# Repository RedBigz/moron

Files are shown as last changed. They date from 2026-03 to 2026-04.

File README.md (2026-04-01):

<p align="center">
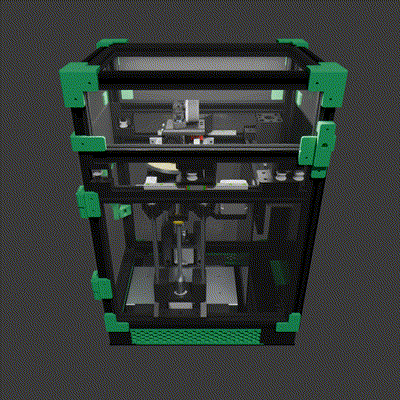
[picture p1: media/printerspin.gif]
    
</p>

<h1 align="center">Moron - The "Non-Euclidean" "V0"</h1>

| [JOURNAL](JOURNAL.md) *(48.5h)* | ~~[BUILDING JOURNAL](JOURNAL_BUILDING.md)~~ | [BOM](BOM.csv) |
|---|---|---|

# Introduction

Hello! I'm May, and you're witnessing the best creation known to man. I don't know how I'm getting a grant for this, but free printer money is free printer money.

> firmware would be an absolute mess<br>
> \- Anicetus 2026

The Moron is a Polar-CoreXY hybrid printer that looks like a V0. I call it "non-euclidean" because I plan to use the polar bed for arc moves -- therefore the best distance between two points is not a straight line.

I wanted something silly that could print ASA and mess around with. Sporting a 120mm polar bed and a 120x120x120 volume, what is there to not like? I haven't written the kinematics yet in software (famous last words -- and I kind of need the printer to do that lol), but right now I bet you could get some really cool timelapses!

My aim for the project is to design a very... odd, printer haha. I also need an enclosed printer for ASA among other things, so this would be a very big help for future projects!

If you want to build one: *don't*. But if you're redbigz you can find all the subtractive cuts/heater files in `cad/cuts/` and `cad/pcb/` and the CAD link [here](https://cad.onshape.com/documents/feabf94b86e21fadd98f4223/w/96543d883315d41072e87b21/e/ef18f69e66a19900010b1f70) (oh also the final STEP is in `cad/`!).

**Forgot to mention this, but please check out the [Voron V0](https://vorondesign.com/voron0.2)! It was a massive inspiration when designing the Moron (from the frame to the electronic placement), so it deserve credit.**

# Render Gallery

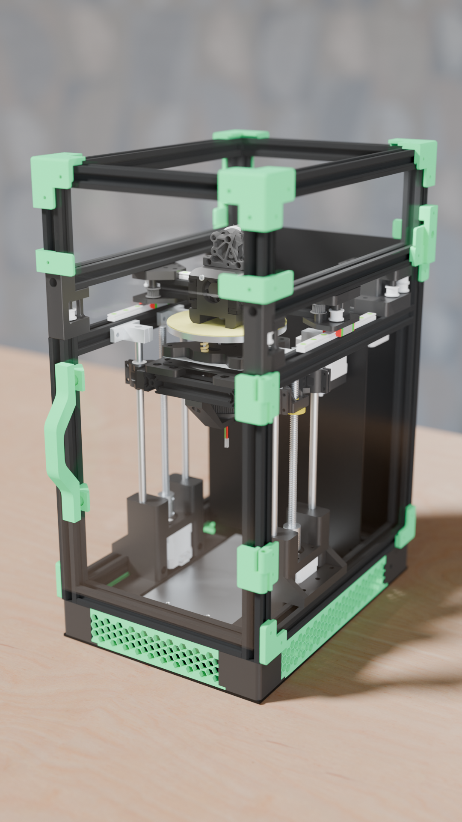
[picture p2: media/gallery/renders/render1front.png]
Render 1 - Front

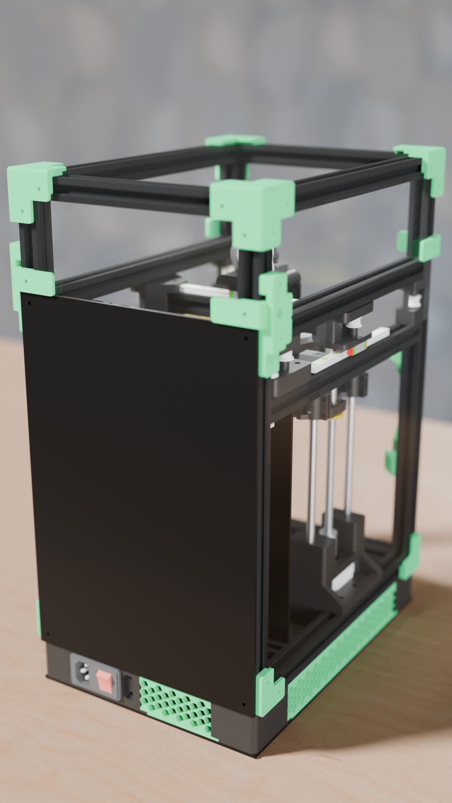
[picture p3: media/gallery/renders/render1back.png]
Render 1 - Back


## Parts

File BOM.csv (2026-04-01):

Category | Cat. 2 | Product | Size | Sourcing Method | Price (USD) | Shipping (USD) | GST (USD) | Qty | Total (USD) | Link | % of Grant | Grant Money Left | % of Grant Money Left
Exterior |  |  |  |  |  |  |  |  |  |  | 0.00% | $350.00 | 100.00%
 | Panels |  |  |  |  |  |  |  |  |  | 0.00% | $350.00 | 100.00%
 |  | Acrylic | 860x630mm | Self | $0.00 | $0.00 | $0.00 | 1 | $0.00 |  | 0.00% | $350.00 | 100.00%
 |  | Flute Board | 900x600mm | Self | $0.00 | $0.00 | $0.00 | 1 | $0.00 |  | 0.00% | $350.00 | 100.00%
 | Etc. |  |  |  |  |  |  |  |  |  | 0.00% | $350.00 | 100.00%
 |  | Magnet | 10x2mm | AliExpress | $5.60 | $0.00 | $0.56 | 1 | $6.16 | https://www.aliexpress.com/item/1005011864346920.html | 1.76% | $343.84 | 98.24%
Internals |  |  |  |  |  |  |  |  |  |  | 0.00% | $343.84 | 98.24%
 | Frame |  |  |  |  |  |  |  |  |  | 0.00% | $343.84 | 98.24%
 |  | Gantry Extrusions | 1600mm |  |  |  |  |  |  |  | 0.00% | $343.84 | 98.24%
 |  | Bed Extrusions | 400mm |  |  |  |  |  |  |  | 0.00% | $343.84 | 98.24%
 |  | Main Extrusions | 2250mm |  |  |  |  |  |  |  | 0.00% | $343.84 | 98.24%
 |  | Top Hat Extrusions | 1400mm |  |  |  |  |  |  |  | 0.00% | $343.84 | 98.24%
 |  | Total Extrusions | 4800mm | AliExpress | $48.61 | $4.35 | $5.30 | 1 | $58.26 | https://www.aliexpress.com/item/1005003428294239.html | 16.64% | $285.58 | 81.60%
 |  |  | 900mm | Self | $0.00 | $0.00 | $0.00 | 1 | $0.00 |  | 0.00% | $285.58 | 81.60%
 |  | T-Nut (30pcs/lot) | M3 | AliExpress | $3.38 | $0.00 | $0.34 | 2 | $7.44 | https://www.aliexpress.com/item/1005010661007823.html | 2.12% | $278.15 | 79.47%
 |  |  | M5 | Self | $0.00 | $0.00 | $0.00 | 2 | $0.00 |  | 0.00% | $278.15 | 79.47%
 |  | Furniture Pad Sheet | ? | Self | $0.00 | $0.00 | $0.00 | 1 | $0.00 |  | 0.00% | $278.15 | 79.47%
 |  |  |  |  |  |  |  |  |  |  | 0.00% | $278.15 | 79.47%
 | Gantry |  |  |  |  |  |  |  |  |  | 0.00% | $278.15 | 79.47%
 |  | Idlers | 20TW6B5 | Self | $0.00 | $0.00 | $0.00 | 1 | $0.00 |  | 0.00% | $278.15 | 79.47%
 |  |  | 20TW6B5 | AliExpress | $6.06 | $0.00 | $0.61 | 1 | $6.67 | https://www.aliexpress.com/item/1005007557987612.html | 1.90% | $271.48 | 77.57%
 |  | Pulleys | 6mm | Self | $0.00 | $0.00 | $0.00 | 1 | $0.00 |  | 0.00% | $271.48 | 77.57%
 |  | Dowel Pins | M5 | Self | $0.00 | $0.00 | $0.00 | 1 | $0.00 |  | 0.00% | $271.48 | 77.57%
 |  | Linear Rail | MGN9H 150mm | AliExpress | $11.21 | $0.00 | $1.12 | 3 | $36.99 | https://www.aliexpress.com/item/1005008170521006.html | 10.57% | $234.49 | 67.00%
 |  | Timing Belt | 6mm 2m | AliExpress | $2.77 | $0.00 | $0.28 | 1 | $3.05 | https://www.aliexpress.com/item/1005005216868552.html | 0.87% | $231.44 | 66.13%
 |  | Motors | 17HS4401 | AliExpress | $7.48 | $0.00 | $0.75 | 2 | $16.46 | https://www.aliexpress.com/item/1005004586903773.html | 4.70% | $214.99 | 61.42%
 |  |  |  |  |  |  |  |  |  |  | 0.00% | $214.99 | 61.42%
 | Toolhead |  |  |  |  |  |  |  |  |  | 0.00% | $214.99 | 61.42%
 |  | Gearset Kit | - | AliExpress | $13.50 | $0.00 | $1.35 | 1 | $14.85 | https://www.aliexpress.com/item/1005004699143725.html | 4.24% | $200.14 | 57.18%
 |  | Extruder Motor | NEMA14 | AliExpress | $10.66 | $0.00 | $1.07 | 1 | $11.73 | https://www.aliexpress.com/item/1005006423228157.html | 3.35% | $188.41 | 53.83%
 |  | Part Cooling Fan (2pcs/lot) | 3010 | AliExpress | $4.21 | $0.00 | $0.42 | 1 | $4.63 | https://www.aliexpress.com/item/1005009389076562.html | 1.32% | $183.78 | 52.51%
 |  | Heatsink Fan | 3010 Axial | AliExpress | $3.05 | $0.00 | $0.31 | 1 | $3.36 | https://www.aliexpress.com/item/1005008793365820.html | 0.96% | $180.42 | 51.55%
 |  | TZ V6 2.0 | - | AliExpress | $15.33 | $0.00 | $1.53 | 1 | $16.86 | https://www.aliexpress.com/item/1005011904542108.html | 4.82% | $163.56 | 46.73%
 |  | BiQu Microprobe |  | AliExpress | $18.32 | $0.00 | $1.83 | 1 | $20.15 | https://www.aliexpress.com/item/1005006314165426.html | 5.76% | $143.41 | 40.97%
 |  |  |  |  |  |  |  |  |  |  | 0.00% | $143.41 | 40.97%
 | Z Axis |  |  |  |  |  |  |  |  |  | 0.00% | $143.41 | 40.97%
 |  | A Motor | 17HS4023 | AliExpress | $5.47 | $0.00 | $0.55 | 1 | $6.02 | https://www.aliexpress.com/item/1005003874936862.html | 1.72% | $137.39 | 39.25%
 |  | Closed Loop Timing Belt | 2GT 6mm 320mm | AliExpress | $4.66 | $0.00 | $0.47 | 1 | $5.13 | https://www.aliexpress.com/item/1005006817234108.html | 1.46% | $132.27 | 37.79%
 |  | Slip Ring | 2.5mm 4CH 5A | AliExpress | $11.25 | $0.54 | $1.18 | 1 | $12.97 | https://www.aliexpress.com/item/1005007456626183.html | 3.71% | $119.30 | 34.08%
 |  | Bed | 120mm (1070 Al) | AliExpress | $9.77 | $0.00 | $0.98 | 1 | $10.75 |  | 3.07% | $108.55 | 31.01%
 |  | Heater |  | JLC | $3.00 | $6.00 | $0.00 | 1 | $9.00 |  | 2.57% | $99.55 | 28.44%
 |  | Bed Springs | ? | AliExpress | $2.90 | $0.00 | $0.29 | 1 | $3.19 | https://www.aliexpress.com/item/1005010253928500.html | 0.91% | $96.36 | 27.53%
 |  | Lead Screw | - | Self | $0.00 | $0.00 | $0.00 | 1 | $0.00 |  | 0.00% | $96.36 | 27.53%
 |  | Coupler | SK8 | Printed | $0.00 | $0.00 | $0.00 | 1 | $0.00 |  | 0.00% | $96.36 | 27.53%
 |  | Smooth Rods | - | Self | $0.00 | $0.00 | $0.00 | 1 | $0.00 |  | 0.00% | $96.36 | 27.53%
 |  | Bearings (4pcs/lot) | LM8UU | AliExpress | $10.56 | $0.00 | $1.06 | 1 | $11.62 | https://www.aliexpress.com/item/1005009031115995.html | 3.32% | $84.74 | 24.21%
 |  | Lazy Susan | 4” | AliExpress | $3.30 | $0.00 | $0.33 | 1 | $3.63 | https://www.aliexpress.com/item/4001325945215.html | 1.04% | $81.11 | 23.18%
 |  | Round PEI Sheet | 120mm + Base | AliExpress | $14.36 | $0.00 | $1.44 | 1 | $15.80 | https://www.aliexpress.com/item/1005006173526115.html | 4.51% | $65.32 | 18.66%
 |  | Silicone Wire | 16AWG 2M | AliExpress | $3.83 | $0.00 | $0.38 | 1 | $4.21 | https://www.aliexpress.com/item/1005008563402600.html | 1.20% | $61.11 | 17.46%
 |  | Z Motors | 17HS4401 | Self | $0.00 | $0.00 | $0.00 | 2 | $0.00 |  | 0.00% | $61.11 | 17.46%
 |  |  |  |  |  |  |  |  |  |  | 0.00% | $61.11 | 17.46%
 | Electronics |  |  |  |  |  |  |  |  |  | 0.00% | $61.11 | 17.46%
 |  | Mean Well LRS-350 | 24V | AliExpress | $30.63 | $2.16 | $3.28 | 1 | $36.07 | https://www.aliexpress.com/item/1005005439330497.html | 10.31% | $25.04 | 7.15%
 |  | TMC2209 (6pcs/lot) | - | AliExpress | $21.40 | $0.00 | $2.14 | 1 | $23.54 | https://www.aliexpress.com/item/33028050145.html | 6.73% | $1.50 | 0.43%
 |  | Mellow FLY D7 | - | AliExpress | $22.84 | $0.00 | $2.28 | 1 | $25.12 | https://www.aliexpress.com/item/1005006422323624.html | 7.18% | -$23.63 | -6.75%
 |  | USB C Mount | 50cm | AliExpress | $2.80 | $0.00 | $0.28 | 1 | $3.08 | https://www.aliexpress.com/item/1005007625403004.html | 0.88% | -$26.71 | -7.63%
 |  | Electronics Fan | ? | Self | $0.00 | $0.00 | $0.00 | 1 | $0.00 |  | 0.00% | -$26.71 | -7.63%
 |  |  |  |  |  |  |  |  |  |  | 0.00% | -$26.71 | -7.63%
 | Fasteners |  |  |  |  |  |  |  |  |  | 0.00% | -$26.71 | -7.63%
 |  | Fasteners | M2.5x8mm | AliExpress | $1.76 | $0.00 | $0.18 | 1 | $1.94 | https://www.aliexpress.com/item/1005005070119421.html | 0.55% | -$28.64 | -8.18%
 |  |  | M3/M4/M5 | Self | $0.00 | $0.00 | $0.00 | ? | $0.00 |  | 0.00% | -$28.64 | -8.18%
 |  | Heated Inserts | M3L3OD4.5 | AliExpress | $3.29 | $0.00 | $0.33 | 1 | $3.62 | https://www.aliexpress.com/item/1005006838108683.html | 1.03% | -$32.26 | -9.22%
 |  |  | M4L4OD6 | AliExpress | $4.87 | $0.00 | $0.49 | 1 | $5.36 |  | 1.53% | -$37.62 | -10.75%
 |  |  |  |  |  |  |  |  |  |  | 0.00% | -$37.62 | -10.75%
Other |  |  |  |  |  |  |  |  |  |  | 0.00% | -$37.62 | -10.75%
 | Tools |  |  |  |  |  |  |  |  |  | 0.00% | -$37.62 | -10.75%
 |  | Tap | M5x0.8mm | AliExpress | $2.45 | $0.00 | $0.25 | 1 | $2.70 | https://www.aliexpress.com/item/33056326494.html | 0.77% | -$40.32 | -11.52%
 |  |  |  |  |  |  |  |  |  |  | 0.00% | -$40.32 | -11.52%
 | Filament |  |  |  |  |  |  |  |  |  | 0.00% | -$40.32 | -11.52%
 |  | PETG (I know I should use ASA but I don’t have a good space to print it) | Black | Self | $0.00 | $0.00 | $0.00 | 1 | $0.00 |  | 0.00% | -$40.32 | -11.52%
 |  | PLA+ (external use only) | Mint Green | Self | $0.00 | $0.00 | $0.00 | 1 | $0.00 |  | 0.00% | -$40.32 | -11.52%
 |  | Bowden Tube | 1.75mm 1M | Self | $0.00 | $0.00 | $0.00 | 1 | $0.00 |  | 0.00% | -$40.32 | -11.52%
Total |  |  |  |  |  |  |  |  | $390.32
Grant |  |  |  |  |  |  |  |  | $350.00
Out-of-Pocket |  |  |  |  |  |  |  |  | $40.32

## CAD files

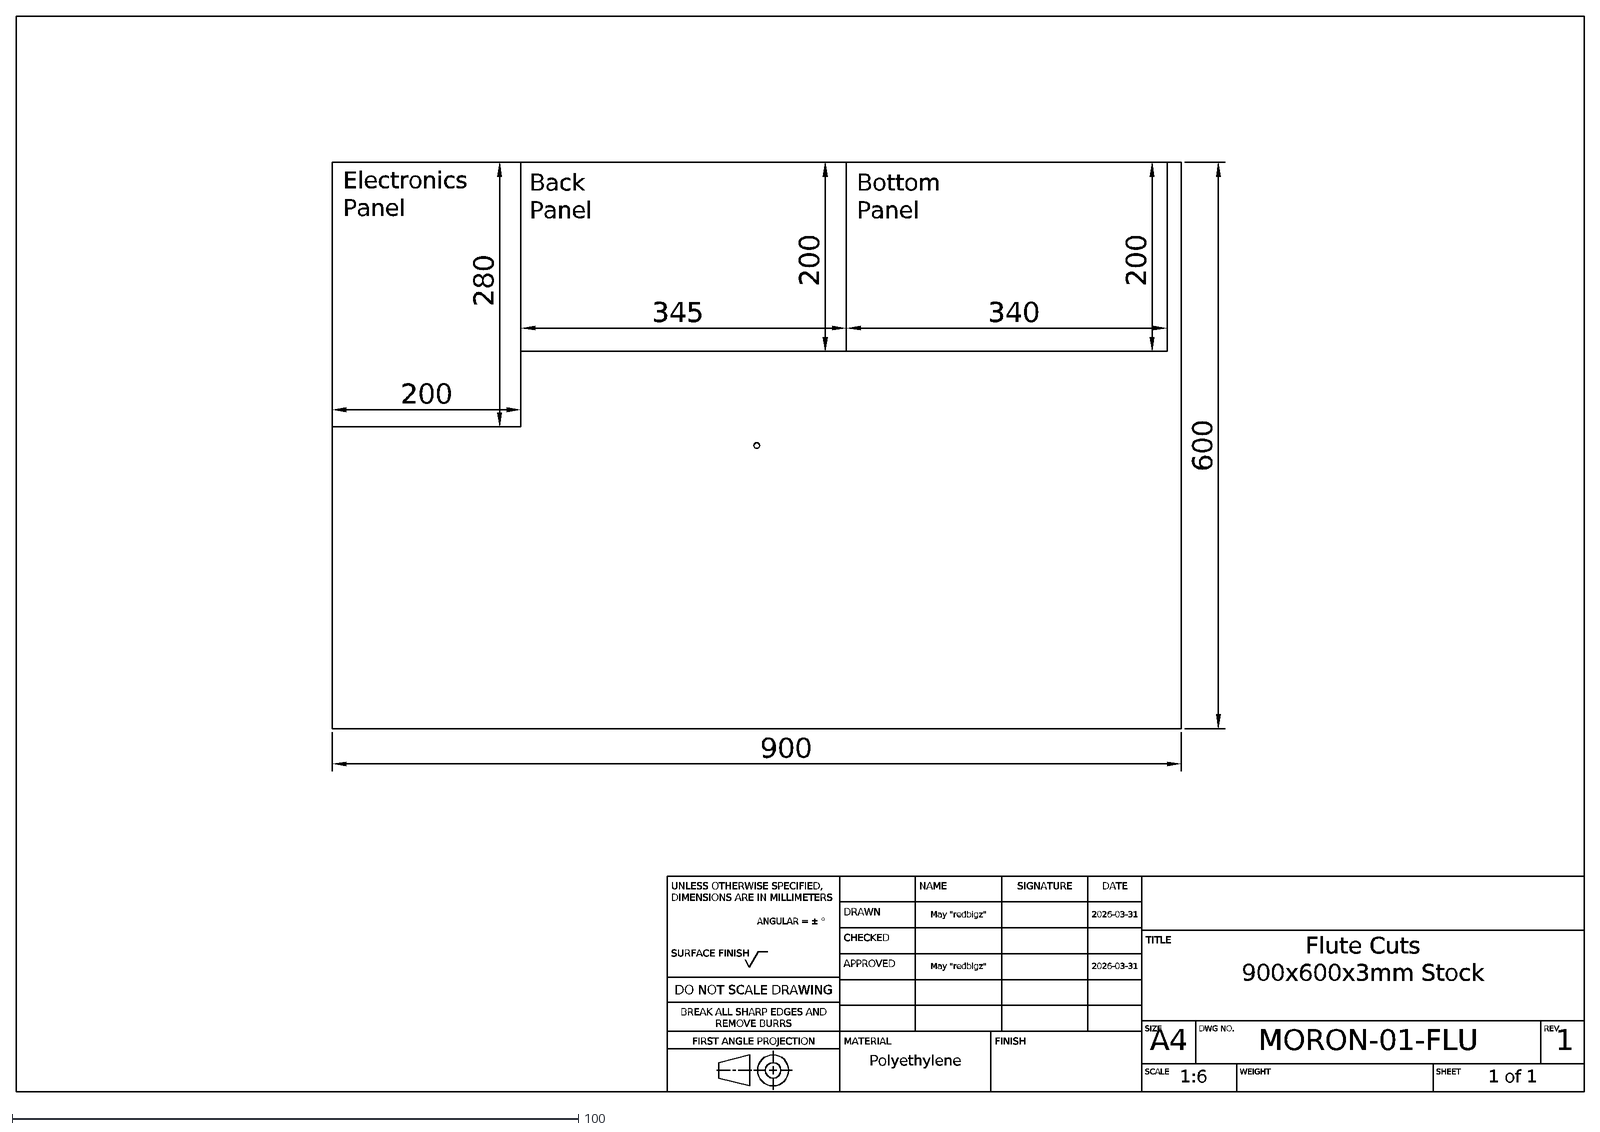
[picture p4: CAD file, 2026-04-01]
cad/cuts/Flute Cuts.dxf
UNLESS OTHERWISE SPECIFIED, DIMENSIONS ARE IN MILLIMETERS
ANGULAR = ± °
SURFACE FINISH
DO NOT SCALE DRAWING
BREAK ALL SHARP EDGES AND REMOVE BURRS
FIRST ANGLE PROJECTION
SIGNATURE
NAME
DATE
DRAWN
May "redbigz"
2026-03-31
CHECKED
APPROVED
MATERIAL
Polyethylene
FINISH
TITLE
Flute Cuts
900x600x3mm Stock
SIZE
A4
DWG NO.
MORON-01-FLU
REV.
1
SCALE
1:6
WEIGHT
SHEET
1 of 1
600
900
280
200
345
340
Electronics Panel
Back Panel
Bottom Panel

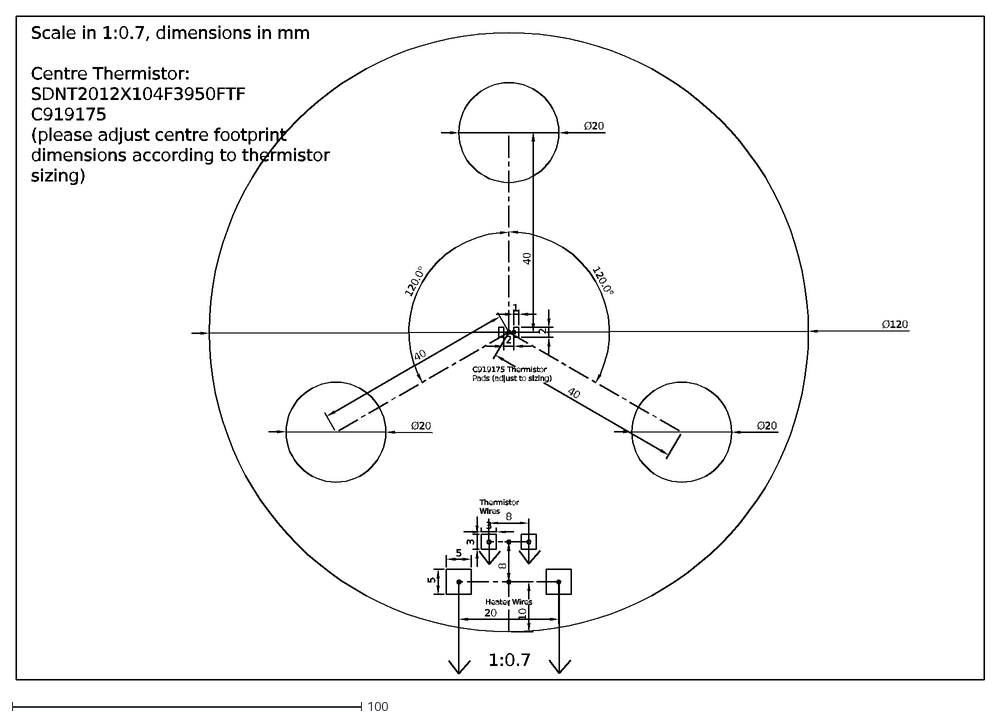
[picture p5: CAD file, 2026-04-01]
cad/pcb/Flex Heater.dxf
1:0.7
10
8
Scale in 1:0.7, dimensions in mm Centre Thermistor: SDNT2012X104F3950FTF C919175 (please adjust centre footprint dimensions according to thermistor sizing)
20
5
3
120.0°
40
Ø20
2
1
Ø120
Thermistor Wires
Heater Wires
C919175 Thermistor Pads (adjust to sizing)

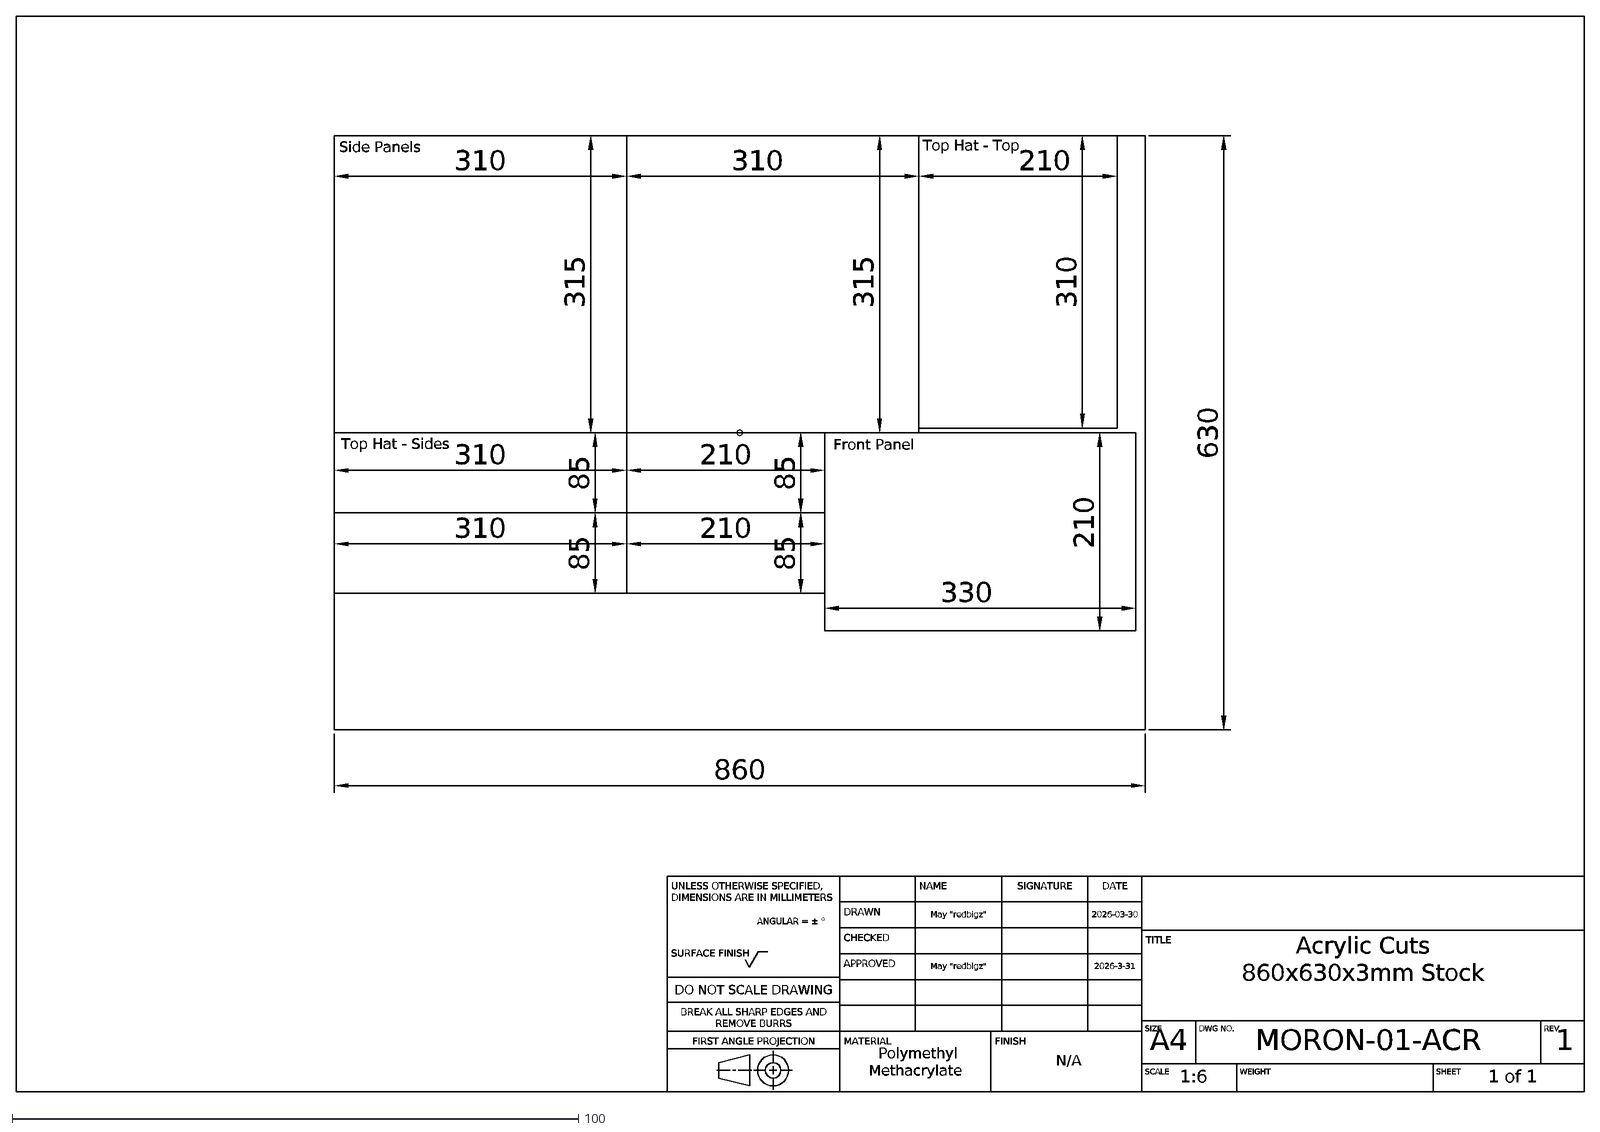
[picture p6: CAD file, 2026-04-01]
cad/cuts/Acrylic Cuts.dxf
UNLESS OTHERWISE SPECIFIED, DIMENSIONS ARE IN MILLIMETERS
ANGULAR = ± °
SURFACE FINISH
DO NOT SCALE DRAWING
BREAK ALL SHARP EDGES AND REMOVE BURRS
FIRST ANGLE PROJECTION
SIGNATURE
NAME
DATE
DRAWN
May "redbigz"
2026-03-30
CHECKED
APPROVED
2026-3-31
MATERIAL
Polymethyl Methacrylate
FINISH
N/A
TITLE
Acrylic Cuts
860x630x3mm Stock
SIZE
A4
DWG NO.
MORON-01-ACR
REV.
1
SCALE
1:6
WEIGHT
SHEET
1 of 1
315
310
860
630
210
330
Top Hat - Sides
Front Panel
Top Hat - Top
Side Panels
85

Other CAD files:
cad/Final Assembly.step

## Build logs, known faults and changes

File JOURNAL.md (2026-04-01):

**Made by**: @redbigz // may<br/>
**Repository link**: https://github.com/RedBigz/moron<br/>
**Total hours so far**: 48.5

- [x] I have a 3D printer or will be getting one before March 21st

# 7/3

## Mind Map

**Approximate hours**: 2

So there used to be an old mind-map here that uses cross-gantry kinematics because I abandoned my plan for a hybrid polar-CoreXY V0-style printer. I just found out it's stupid easy to make a polar bed!

Lazy susans spin infinitely and are relatively cheap (https://www.aliexpress.com/item/1005007540027466.html), so i can just screw some mounts in and have a polar bed! Would still have to devise printed idlers and such though.

Here's my new mind map!

New Mind Map

# 22/3-23/3

## Z Axis

**Approximate hours: 9**

I created the Z axis, including the lazy susan system for the bed.

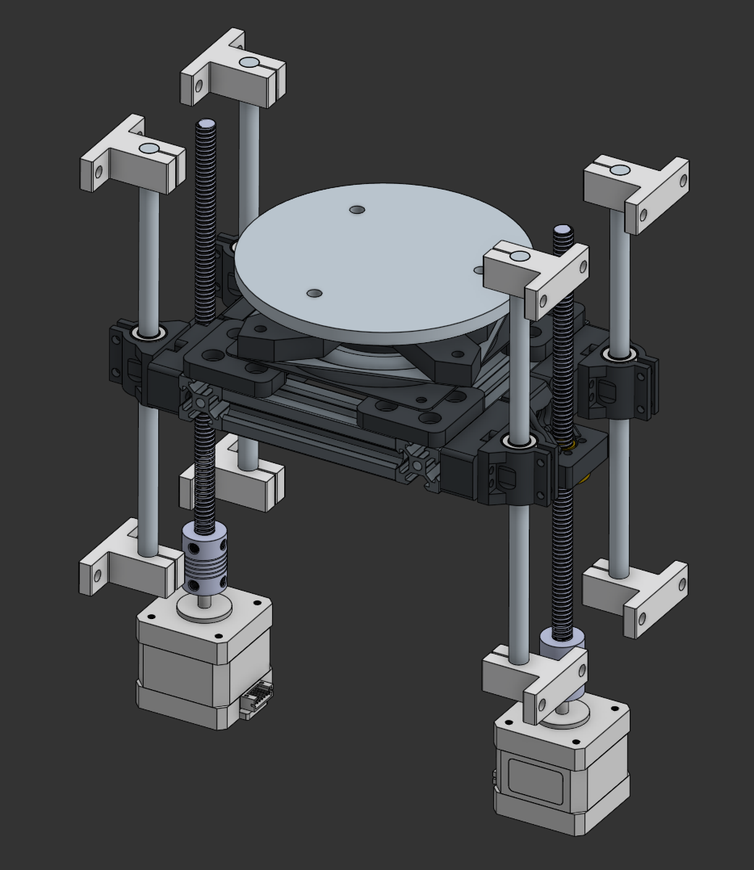
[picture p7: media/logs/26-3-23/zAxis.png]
Z Axis


### Bed

For the bed, I'm planning to CNC a custom 120mm diameter polar bed design (inspired by the V0 120mm plate). I mocked up a basic 6mm three-screw (M3) bedplate in OnShape and created all the necessary adapters to place it on the Z axis. A slip ring mount point was also implemented into the bed adapter to stop wire tangling. I'm using a 4" lazy susan for this as any larger would introduce more issues when mounting (I noticed >4" lazy susans have glued feet as well, which sucks).

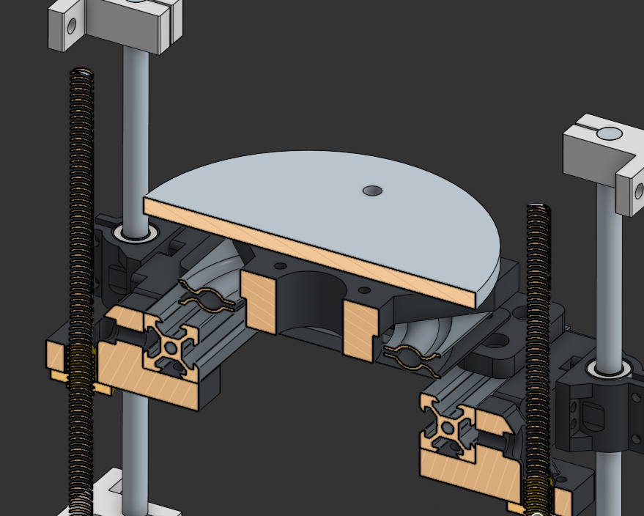
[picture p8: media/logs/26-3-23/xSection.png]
Cross-section of the Z axis


### Motion

I'm using two motors for the Z axis to maintain stability, as I couldn't find a way to implement a cantilever polar bed since the weight requirements would be high.

I have yet to set up the polar rotation system, will do that soon.

That's pretty much it <3

### Rotation

This took forever to set up. I realised that a belt path couldn't be made above the lazy susan, so I elongated the slip ring and added 2GT teeth to allow for rotation *under* the bed.

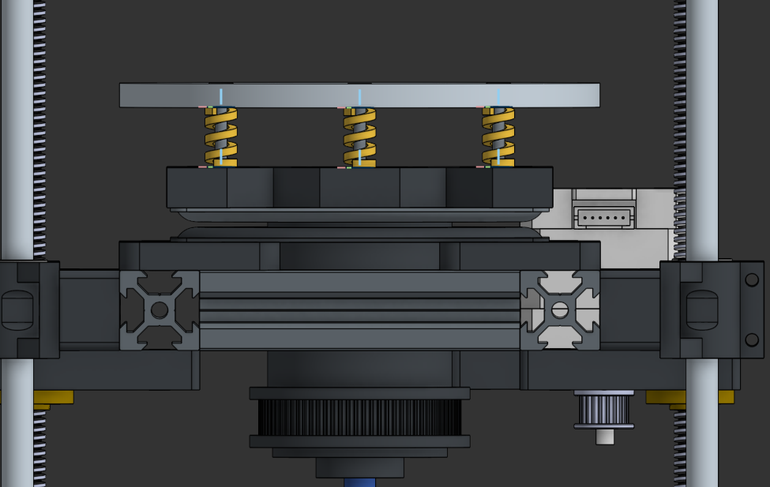
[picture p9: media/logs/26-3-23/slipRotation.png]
Rotation


# 24/3-26/3

## Gantry

**Approximate hours: 9**

I made the gantry! Yay! I ended up using MGN9 rails since linear rods would be annoying to tap, and they're relatively cheap when you get them off sketchy AliExpress stores.

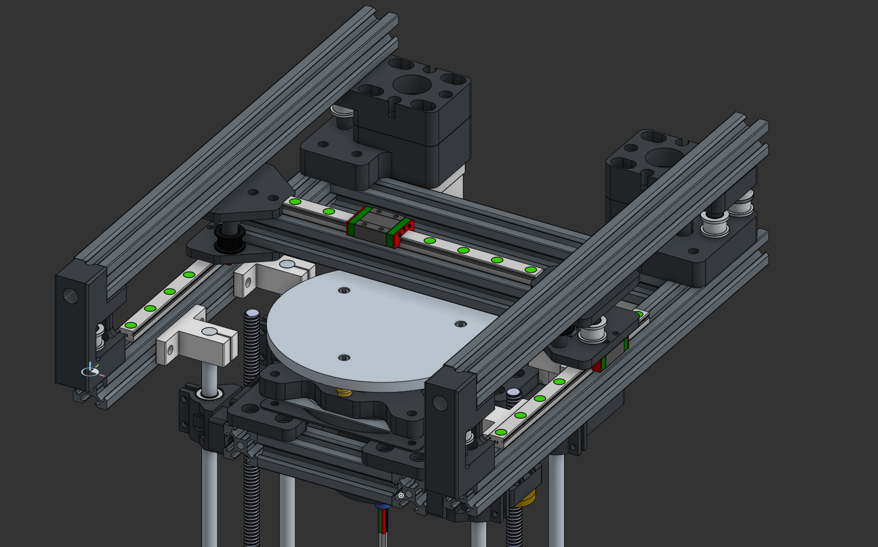
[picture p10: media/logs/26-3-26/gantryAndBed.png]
Gantry and bed


I ripped off the placement style of the idlers and motors from the Voron 0.2 since I barely had space, but all the modelling and calculations were done by me.

**BEHOLD: THE CRAPPY EXCALIDRAW BELT PATH**

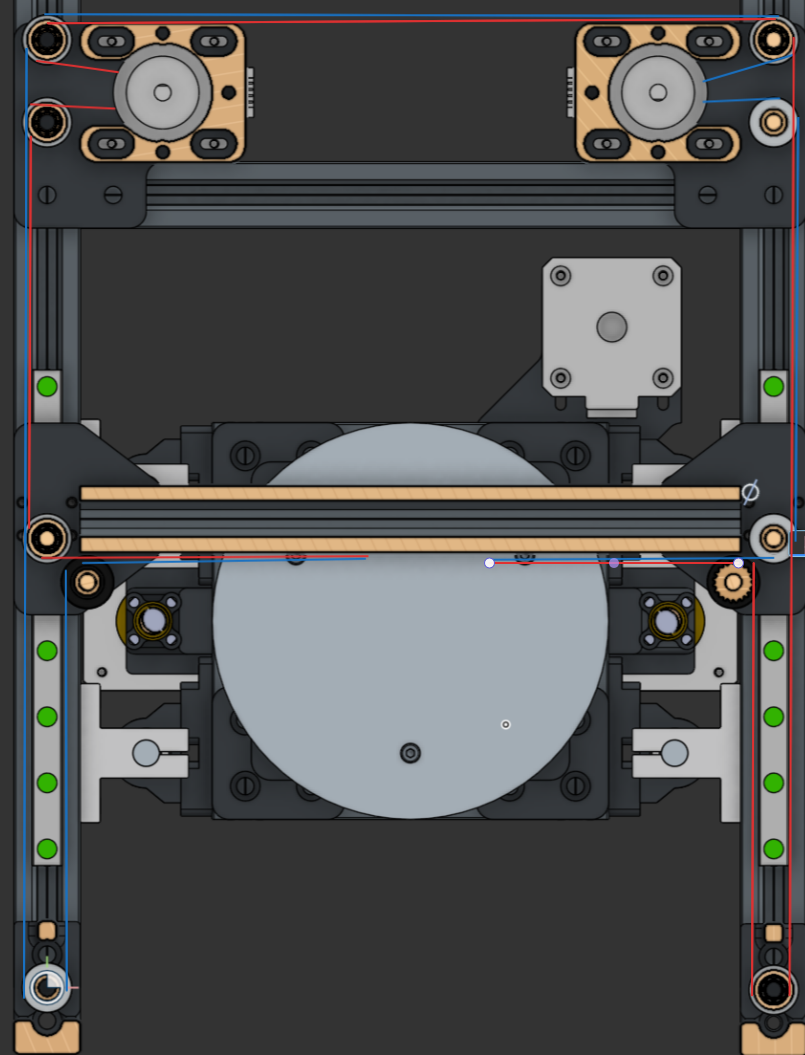
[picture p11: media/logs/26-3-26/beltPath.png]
Belt path


# 26/3-28/3

## Frame

**Approximate hours: 1**

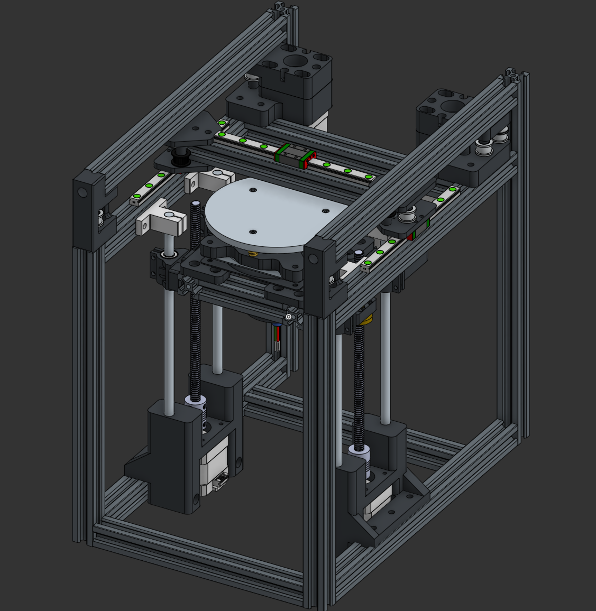
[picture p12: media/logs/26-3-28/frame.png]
Frame


this was pretty boring lmao

I haven't done the top hat yet (seen in V0s -- yeah I'm kind of making this really Vorony [Vorony, Voronic? Eh I dunno]), since that ties in with the bowden system and I want to work on that first.

I had to redo the bottom smooth rod holders. I'm no longer using SK8A mounts on the bottom, in favour of a sturdy printed bracket I made. This was needed as the smooth rods were too short to mount to the bottom of the frame, meaning I would require more aluminium ($$$) to manufacture the printer. These holders also have the added benefit of securing the motors.

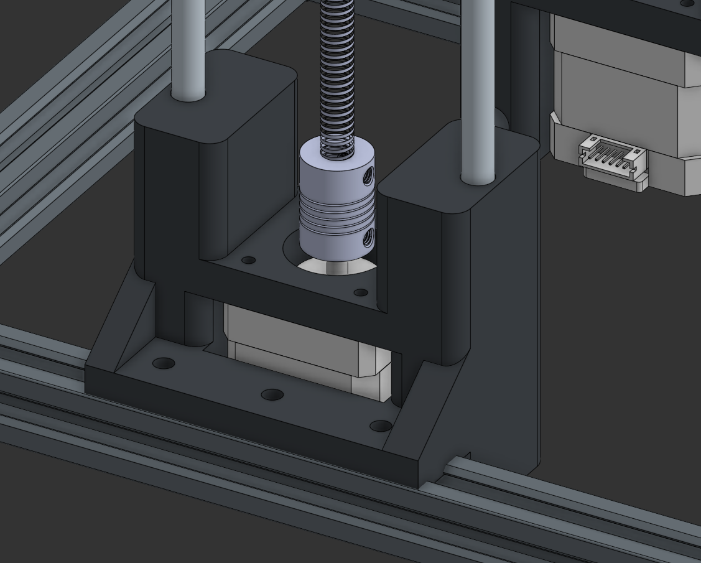
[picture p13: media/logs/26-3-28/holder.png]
Z Holder


## Toolhead

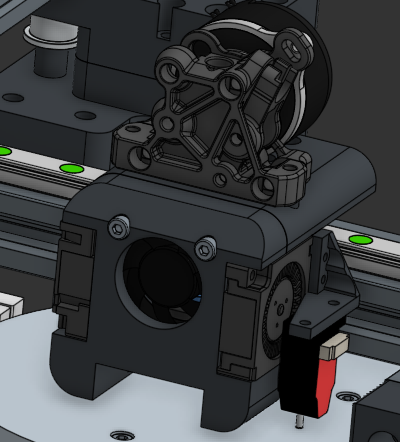
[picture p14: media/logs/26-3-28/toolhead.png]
Toolhead


**Approximate Hours: 7**

i did itttttttt!

This toolhead took forever to make, but it's so worth it! It's running a V1 ProtoXtruder with a TZ E6 2.0 hotend, all in a Dragonburner-style shape! I'm in love <3

I ended up deciding to use two 3010 blowers for part cooling and a 3010 axial for the heatsink. I also tacked on a BiQu microprobe because an Eddy was too big lol

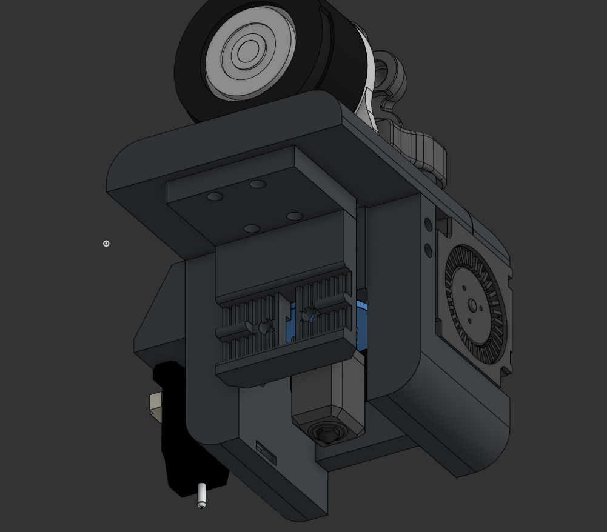
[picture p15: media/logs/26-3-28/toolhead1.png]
Toolhead Back


I'm using an MGN7H carriage for motion, and a simple belt clamp that's parallel to the extrusion.

# 29/3

## Exterior & Electronics

**Approximate Hours: 8**

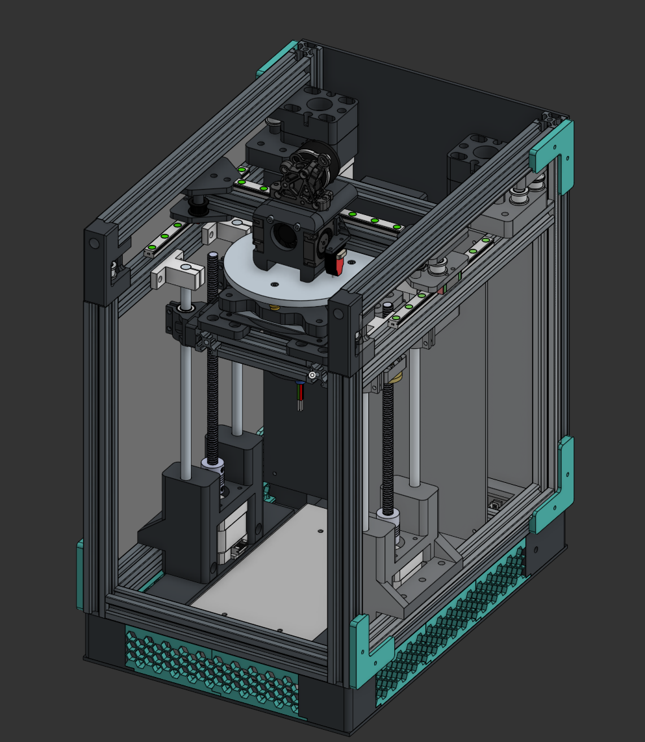
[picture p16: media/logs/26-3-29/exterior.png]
Exterior


hewwo!

this section is *big* so i'm splitting it into two sections:

### Electronics

After talking with WilliamPrime on the Slack channel, I opted for a Mellow FLY D7 mobo! It's super cheap and way smaller than an octopus, so it should work :3. I made a mount on the back for the Fly's profile in hopes that it would mount. Better wait and see.

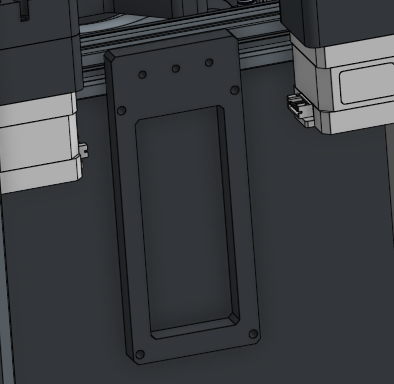
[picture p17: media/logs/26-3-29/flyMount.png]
FLY Mount


I made a mount for the PSU by modifying the motor mounts to allow for an attachment angle bracket to be screwed in. It's a pretty dirty job, but I'm on a time constraint here.

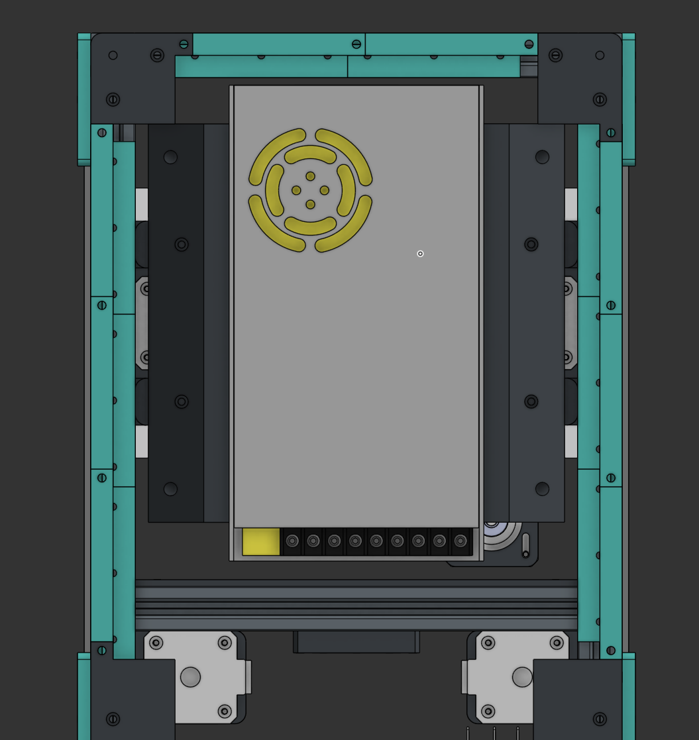
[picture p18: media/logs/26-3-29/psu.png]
Shitty PSU Mount


I also set up an IEC connector on a skirt that I'll use to connect mains.

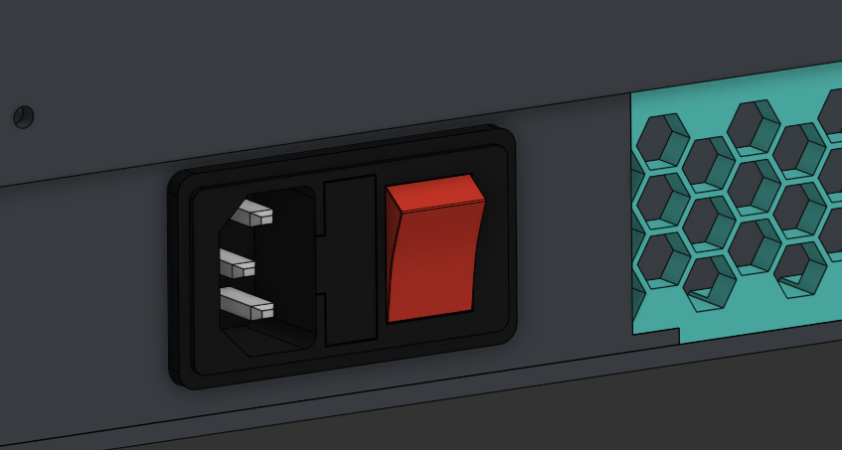
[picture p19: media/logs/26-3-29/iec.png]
IEC Connector

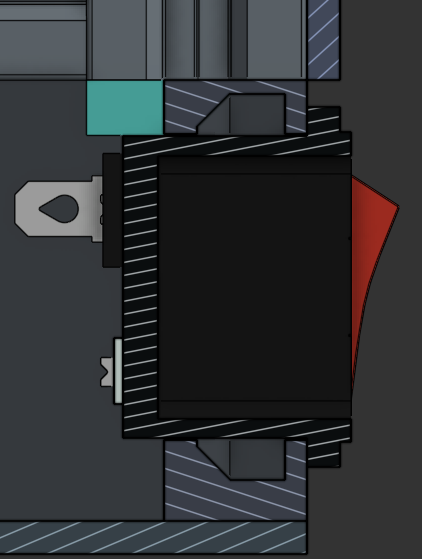
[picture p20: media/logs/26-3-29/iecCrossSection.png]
IEC Connector (Cross Section)


*(snap fits ftw)*

### Exterior

I ended up making primitive corner clips to hold the side acrylic sheets in. I also determined the sizes for the ~~ACM~~ flute sheets for the interior of the printer. I have yet to make the top hat or the front hinge. I think I'll go with a screw-in top hat since a hinge seems difficult to make and work with. I haven't set up a model for the bottom sheet (above the PSU), as I may print that instead -- due to the complicated shape.

*Note from the future (31/3/26): I have swapped to using flute board from ACM! ACM's just so expensive!*

Additionally, I have added a bowden intake on the foot holding the IEC inlet, to allow for easy filament feeding.

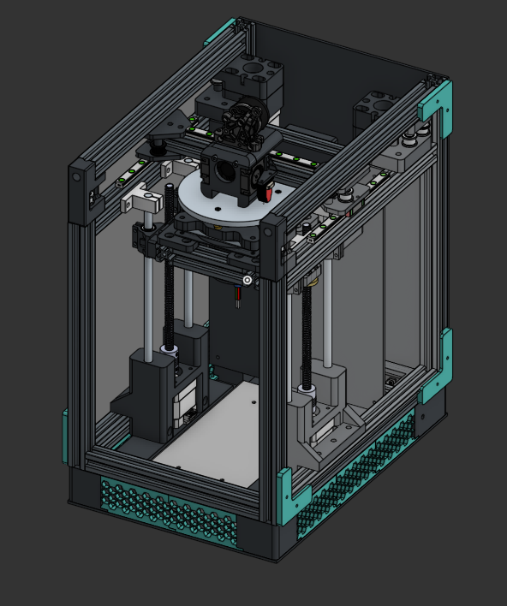
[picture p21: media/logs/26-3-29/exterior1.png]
Exterior Front

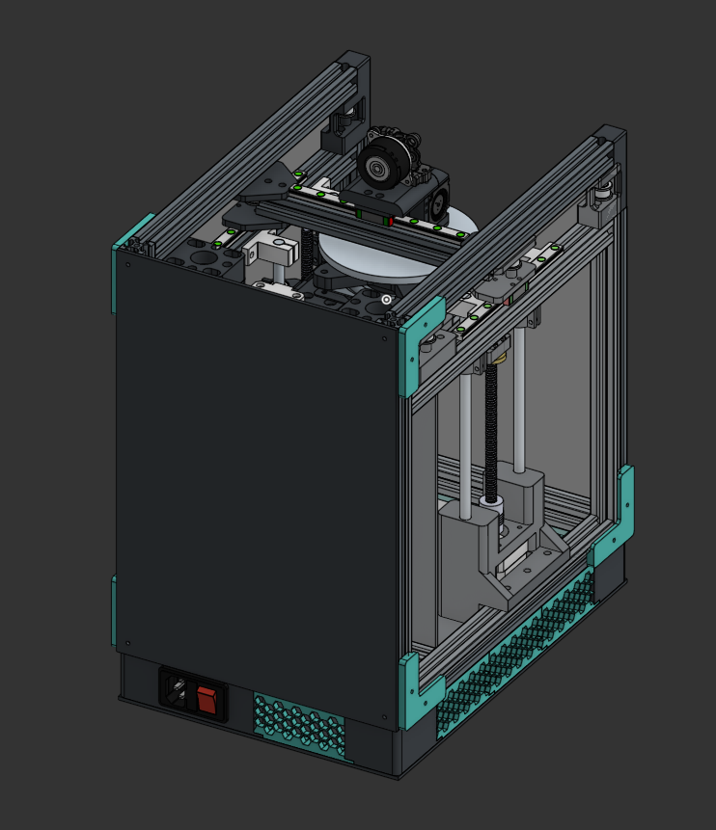
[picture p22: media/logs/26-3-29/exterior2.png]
Exterior Back


# 30/03

## Top Hat and Exterior

**Approximate Hours: 6**

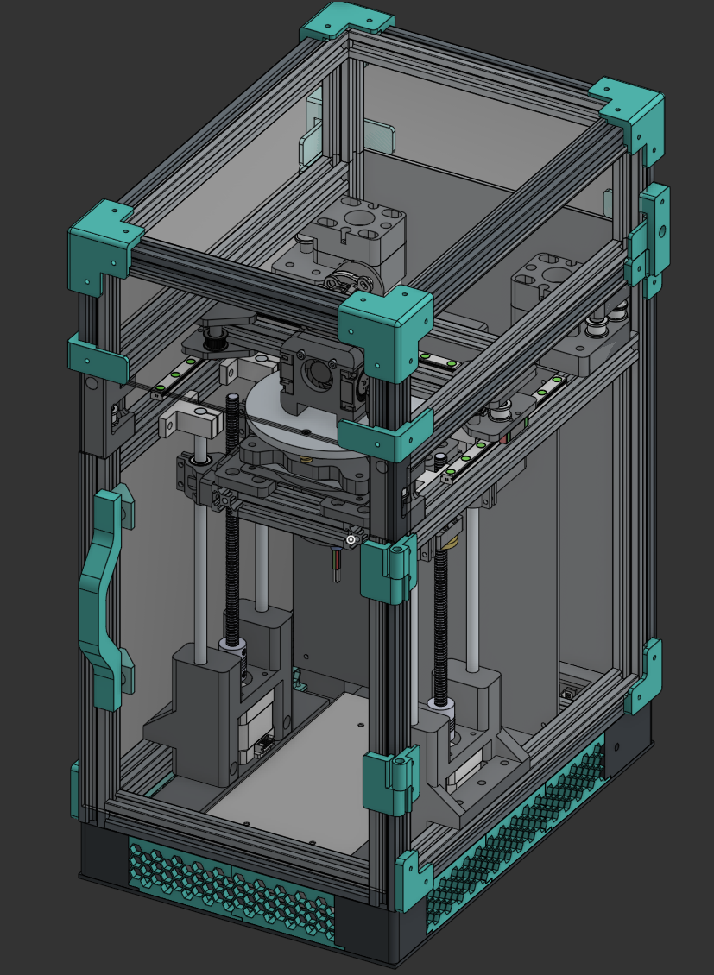
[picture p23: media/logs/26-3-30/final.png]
Front Photo (Final)


I designed an extremely basic top hat to contain the filament Bowden tube. It's nothing special. It's connected via a basic clip that secures it with two M3 fasteners.

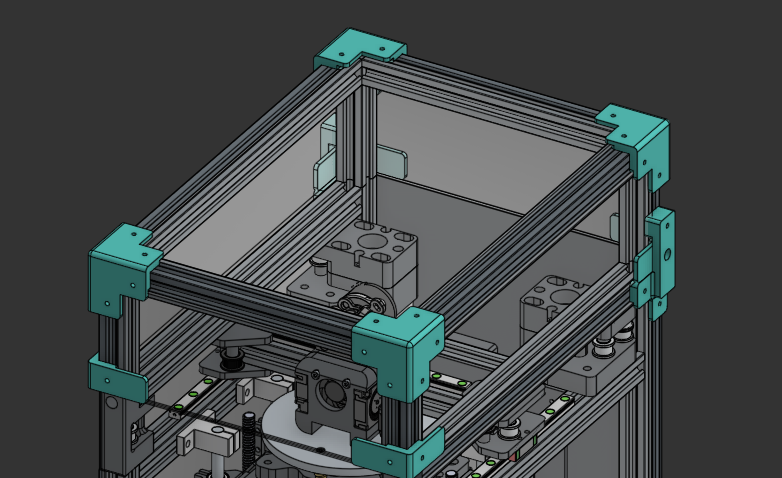
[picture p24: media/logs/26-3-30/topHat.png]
Top Hat


I also created a hinge system for the front panel, using 10x2mm magnets for the handle and basic screw-based hinges.

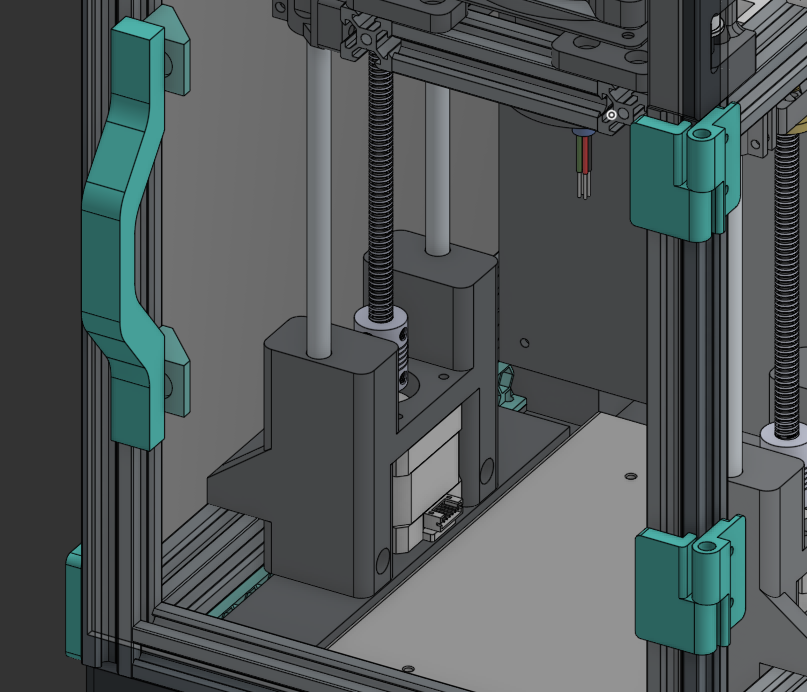
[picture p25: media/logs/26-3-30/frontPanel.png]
Front Panel


## Small Fixes

**Approximate Hours: 0.5**

### Slip Ring Reinforcement

I ended up reinforcing the rotor of the slip ring with a basic bracket, which should hold considering I won't be spinning this bed that fast.

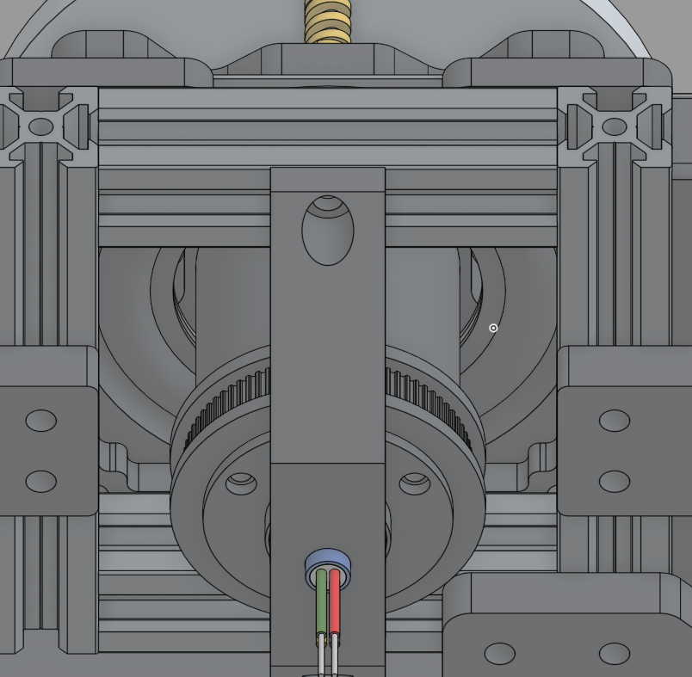
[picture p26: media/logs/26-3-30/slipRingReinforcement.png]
Slip Ring Reinforcement


### USB-C Outlet

In the previous log, I forgot to mention that I would need a USB-C outlet. As I don't have an SBC at the moment, I've decided to use an old laptop or server instead. In that case, I would need a data port running to the exterior of the printer.

Here it is! I found a simple mount online and worked on the profiles. It should hold up well for now, at least.

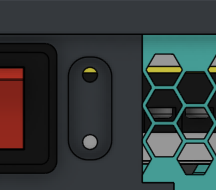
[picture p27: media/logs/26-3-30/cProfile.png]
USB-C Outlet Mount


# 31/03

## BOM

**Approximate Hours: 5**

hewwo!

The BOM is pretty much complete! I had to substitute a LOT of items (such as the CNC bed) since everything's soooo expensive :(. I arrived at an out-of-pocket value of about $40 excluding filament, which is about $59 AUD. Not bad! Check it out [here](BOM.csv).

## Cut Files & Flex Heater

**Approximate Hours: 1**

I made all the cut files for the acrylic and flute board! They're published in the `cad/cuts/` folder in the repo.

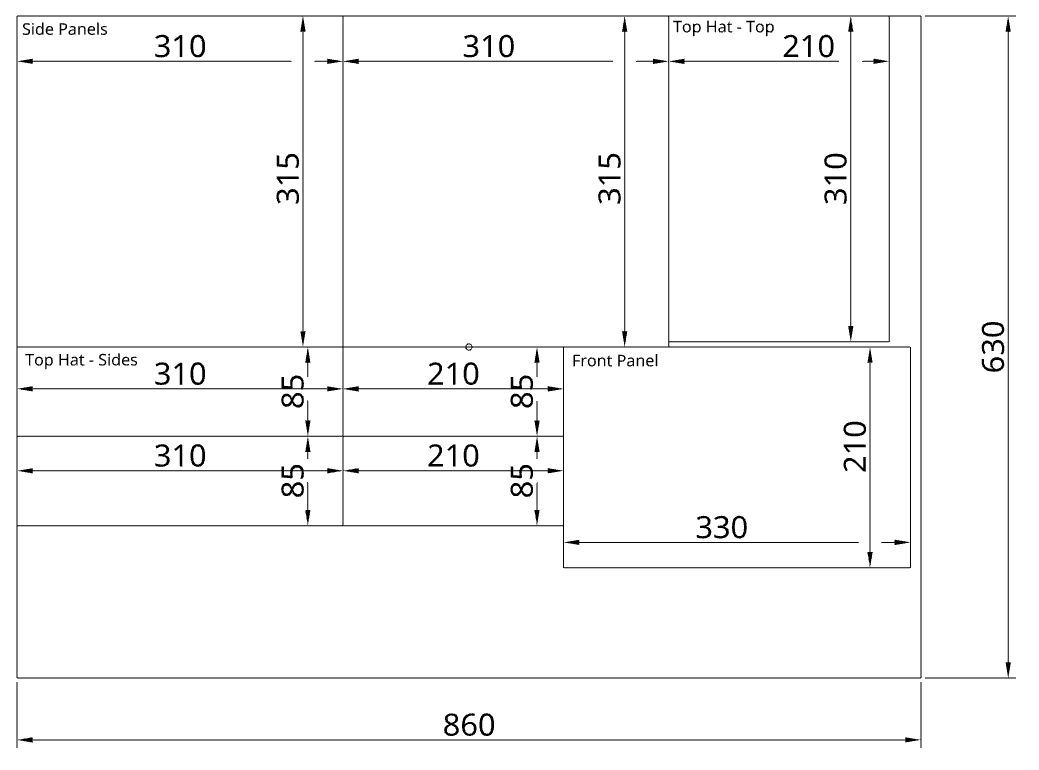
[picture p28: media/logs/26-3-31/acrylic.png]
Acrylic Cuts

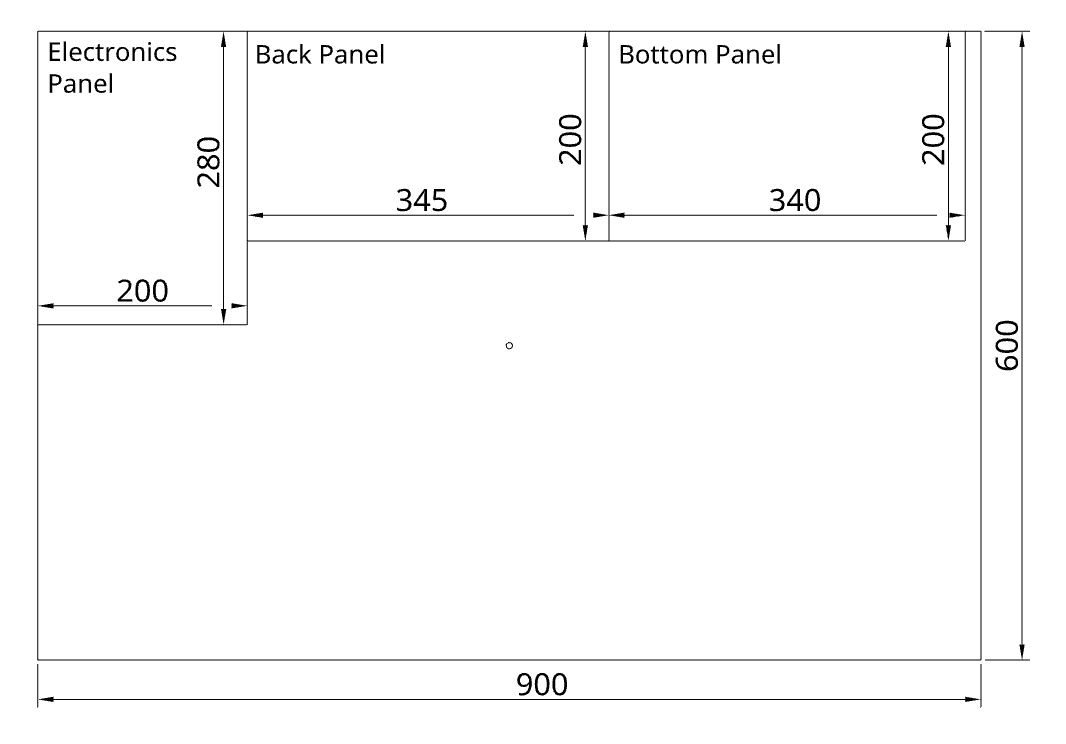
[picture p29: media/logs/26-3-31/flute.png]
Flute Cuts


I also made the flex heater drawing! I'll send it to JLC and they should be able to engineer traces out of it:

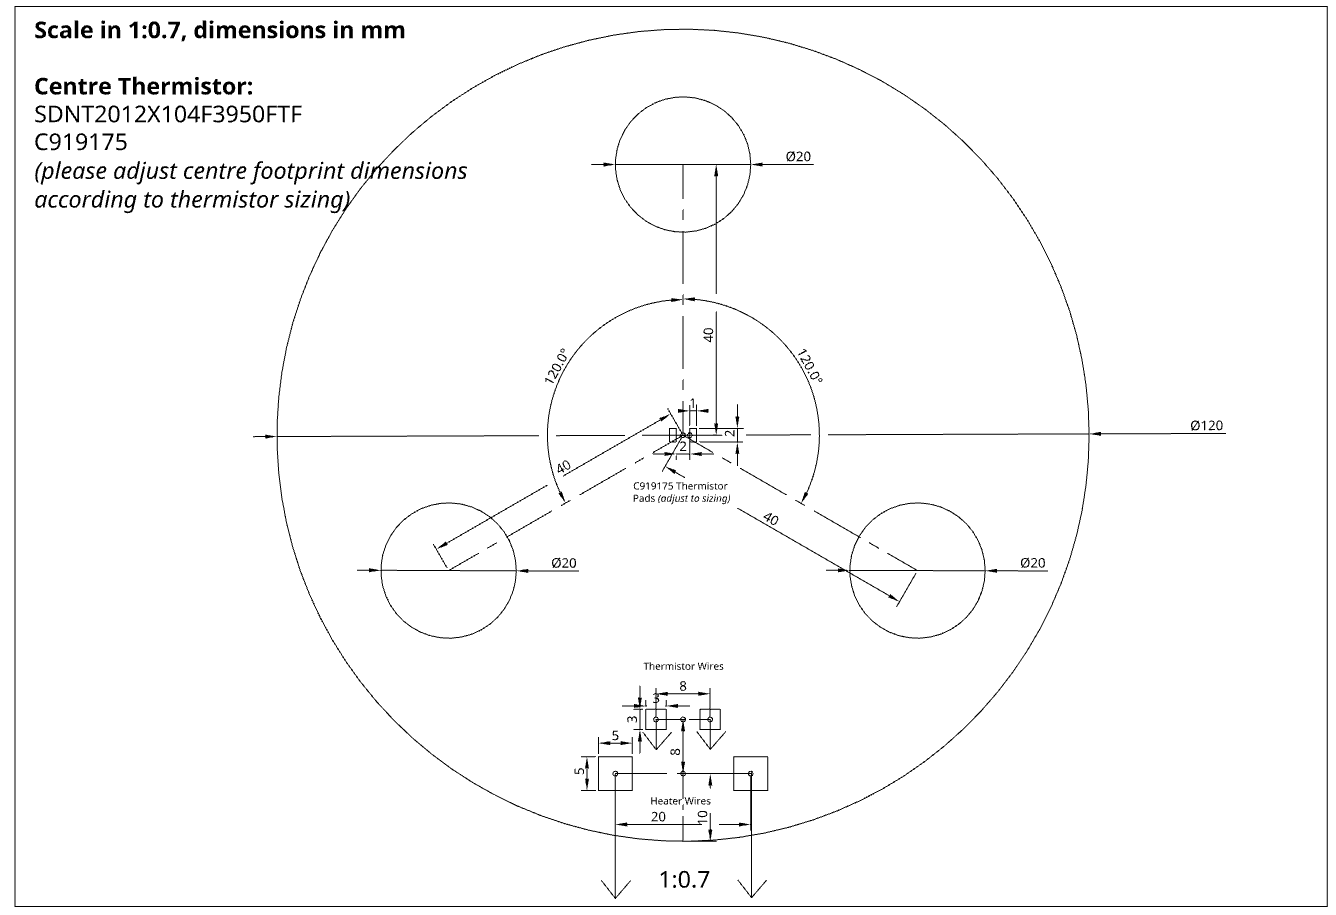
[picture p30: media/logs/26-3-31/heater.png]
Flex Heater


# We're done folks! Check the [building journal](JOURNAL_BUILDING.md) for the rest of the journaling!

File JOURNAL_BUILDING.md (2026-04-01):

## If you're reading this, I haven't started o_o

Check back in a few weeks.

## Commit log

2026-03-23 add journal entry for z axis
2026-03-26 add journal entry for gantry
2026-03-28 add journal entry for frame and toolhead
2026-04-01 finish it off!
    [Acrylic Cuts.dxf, BOM.csv, BOM.ods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]
2026-04-01 add BOM tab to readme
2026-04-01 add bowden tube to BOM csv (not in spreadsheet though)
    [BOM.csv]
